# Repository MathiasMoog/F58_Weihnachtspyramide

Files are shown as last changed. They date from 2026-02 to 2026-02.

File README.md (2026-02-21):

# Antrieb und LED-Kerzen für Weihnachtspyramide

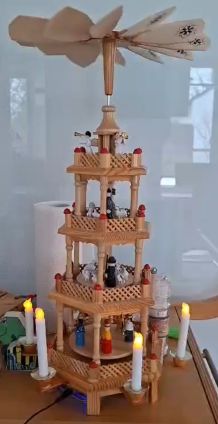
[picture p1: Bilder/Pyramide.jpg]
Weihnachtspyramide


Und als kurzes Video: [Weihnachtspyramide](Bilder/Pyramide.mp4)

## Kurzfassung

Ein Arduino Nano ESP steuert den Antrieb und die LED Kerzen einer Weihnachtspyramide.

Über den ESP wird eine MQTT Anbindung erstellt.

### Hintergrund

Unsere Weihnachtspyramide ist seit einigen Jahren nicht mehr genutzt worden, da niemand Lust hat auf die echten Kerzen aufzupassen. Außerdem läuft sie mit den Kerzen nicht so gut.

In der Bastelkiste hatte ich noch einen (uralten) [Arduino Nano ESP](https://iot.fkainka.de/board) von F. Kainka und aus dem alten Drucker den Antrieb für die Scan Einheit.

### Ordner

- Bilder - Bilder und Zeichnungen
- Druckvorlagen - OpenSCAD Zeichnungen für 3D Drucke 
- PyramidenMQTT - Der Arduino Sketch 
- PyramidenSchaltplan - KiCad Schaltplan und Platine

## Aufbau

Passt es für eure Weihnachtspyramide an, dieser Abschnitt bezieht sich auf meine Pyramide.

### Antrieb 

Mit einem Motor aus der Bastelkiste probiert. Alter Antriebsmotor aus Scanner mit Getriebe. Blech zurecht gesägt. Optische Drehzahlerfassung entfernt. Anstelle Zahnräder, einen Gummiring verwendet. Letztes Zahnrad am Motor geschliffen so dass eine Laufrille für den Gummiring entsteht.  

Adapter von Antriebsstange über Antriebsrad bis Aufnahme in Kugellager, [Antrieb](Druckvorlagen/Antrieb.scad), und eine Kugellager Halterung,[Grundplatte](Druckvorlagen/Grundplatte.scad),  in OpenScad gezeichnet. Druck in PETG. Material ist guter Kompromiss zwischen leicht auf dem alten Creatity Ender druckbar und ausreichender Festigkeit. 

Antrieb                    |  Grundplatte
:-------------------------:|:-------------------------:
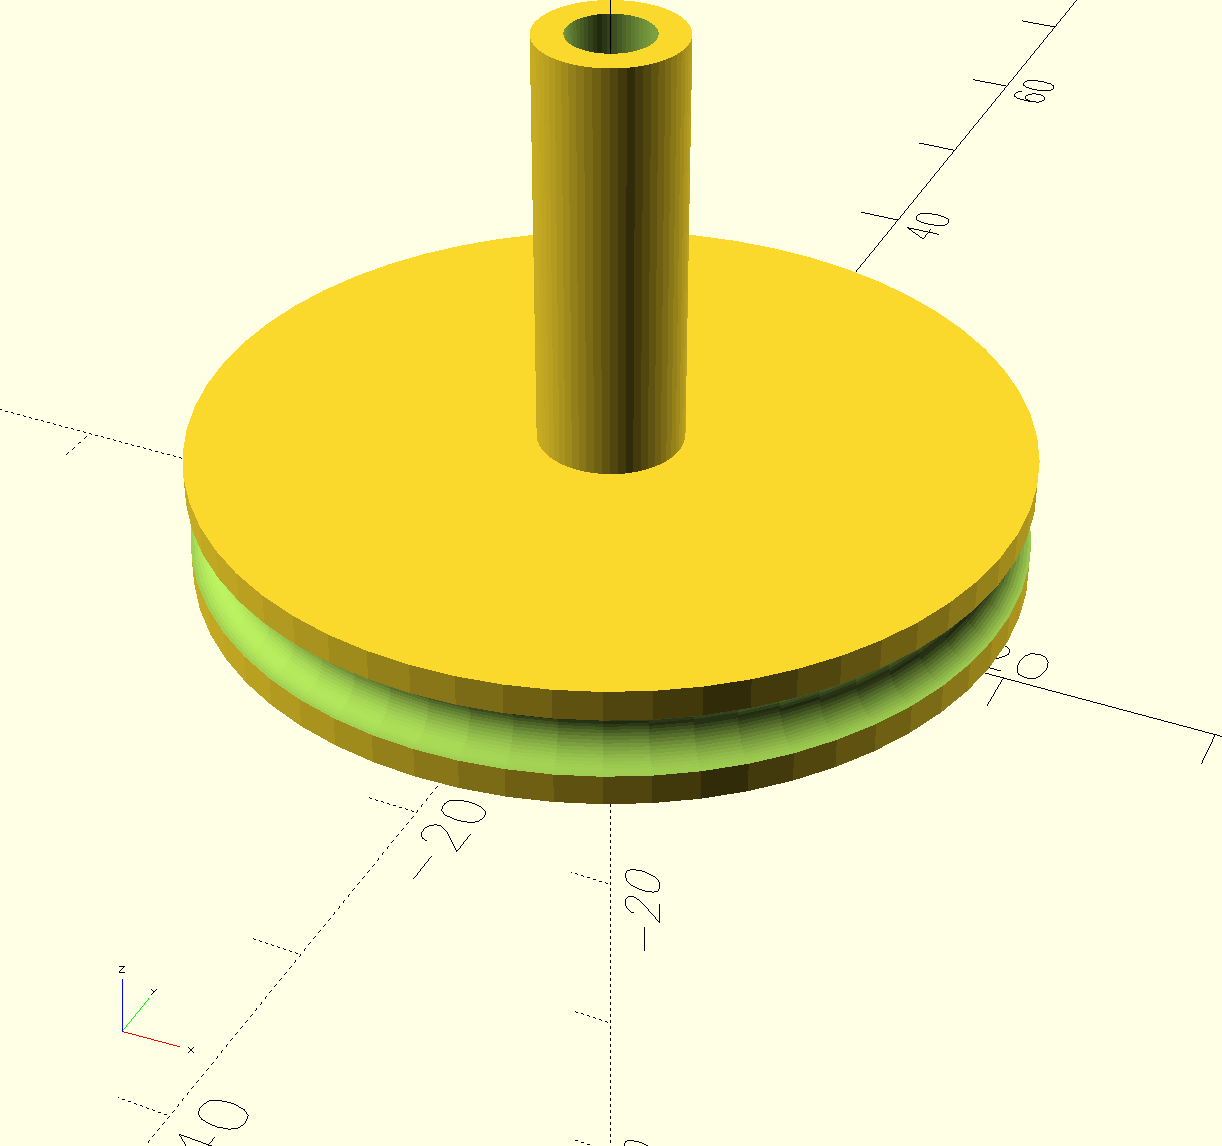
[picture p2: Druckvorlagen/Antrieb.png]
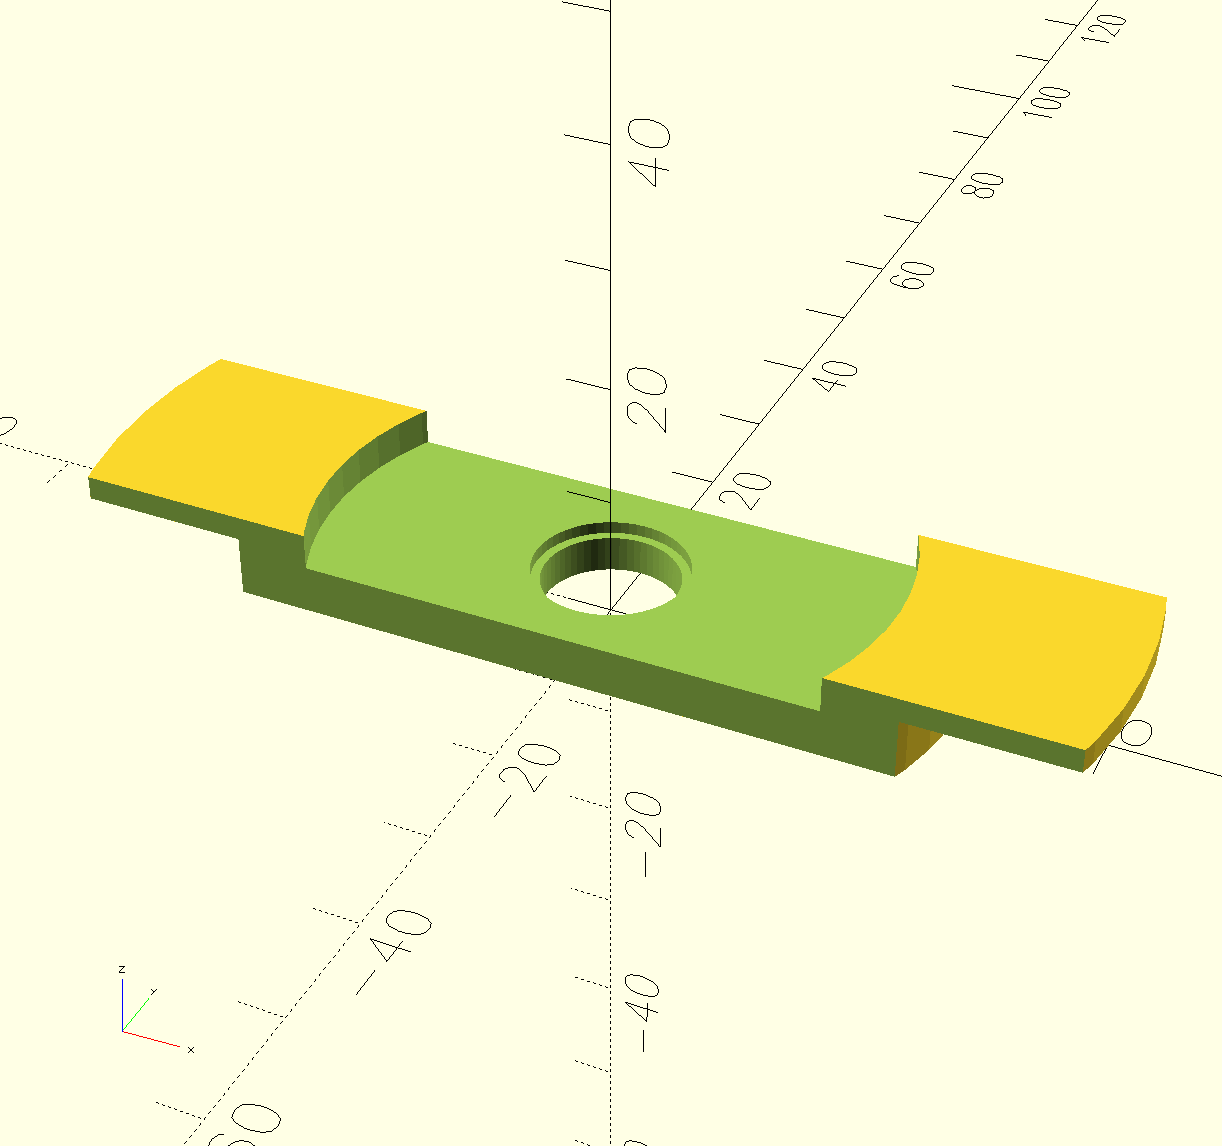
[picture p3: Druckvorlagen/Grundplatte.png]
 | 

Der neue Antrieb ersetzt die alte Lagerung in einer Keramikschale.

Vorher                    |  Nachher
:-------------------------:|:-------------------------:
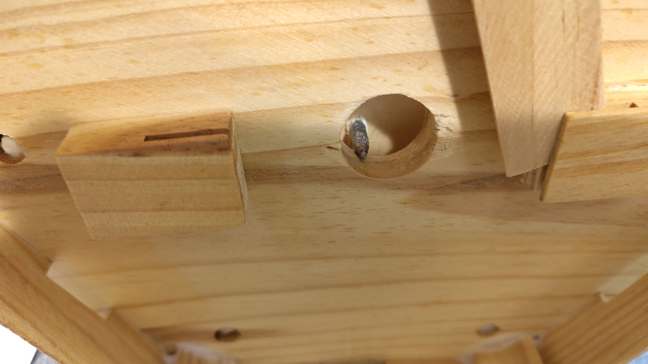
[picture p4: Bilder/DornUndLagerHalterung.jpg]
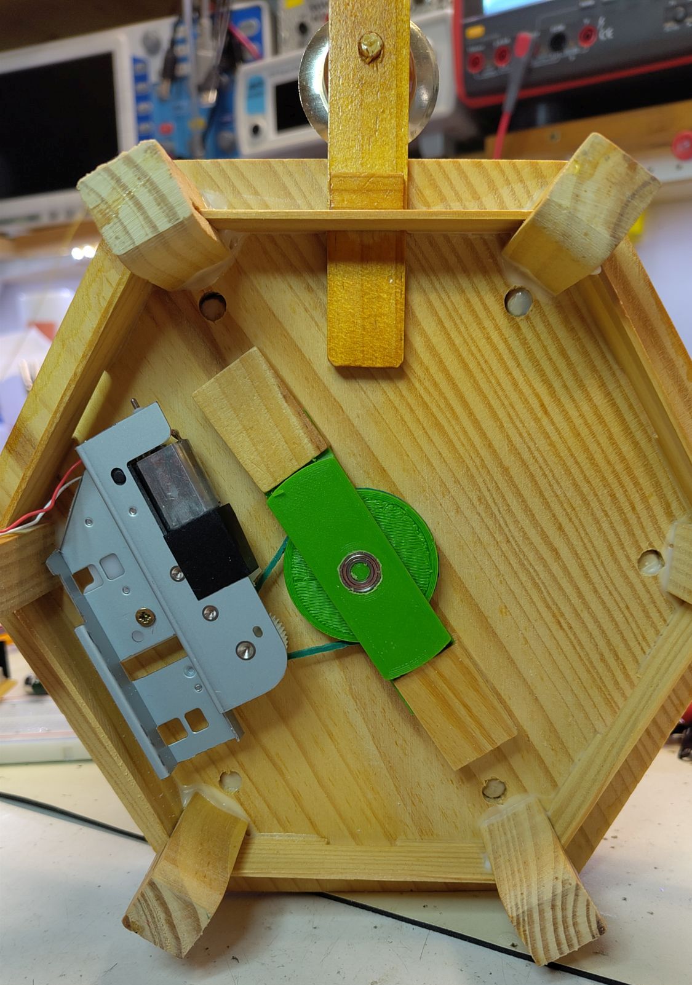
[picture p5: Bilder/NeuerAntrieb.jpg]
 | 

### Ansteuerung des Motors
  
Der Motor läuft ab 2,5 V an. Bilde 0 bis 100 auf 0 + [128, 255] ab. Er nimmt maximal 80 mA auf. Es reicht ein kleiner Transistor zum Schalten.

Aus Bastelkiste BC 639, 1 A maximal, gemessen Verstärkung hFE 100, Datenblatt mindestens 25 bei 5 mA Basisstrom. Auslegung, 560 Ohm Vorwiderstand

### Kerzen

Auf Thingiverse habe ich Kerzen mit schön gestalteten Flammen gefunden. Sie sind Teil eines Weihnachtsbogens [Christmas Light Bow](https://www.thingiverse.com/thing:4674237) von M. Lachmann. Flamme.stl mit transparentem PLA und die Kerzen in weißem PLA gedruckt. 

Kerze.stl hat Original 10 mm Durchmesser. Ich benötige 13 mm. Skaliere in x und y Richtung um 130 %. In x Richtung Skalierung 70, 80, 90, 100, 110, 120 %. Sieht nach ungleichmäßig abgebrannten Kerzen aus.

Löcher in die original Kerzenhalter gebohrt und Kabel durchgeführt:

Kabelführung                    |  Fertige Kerzen
:-------------------------:|:-------------------------:
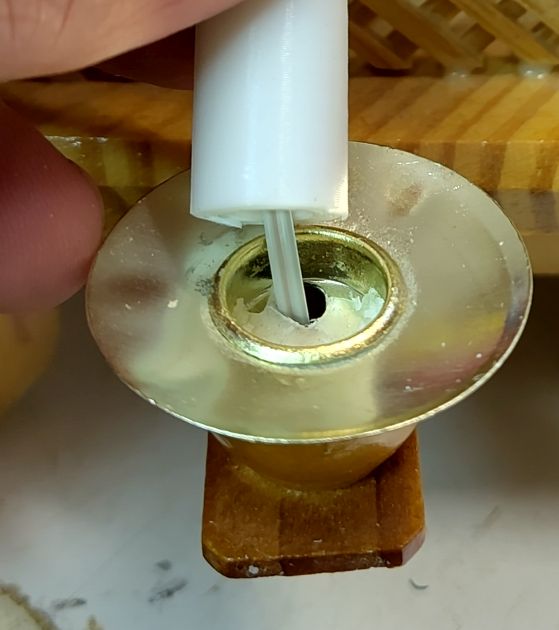
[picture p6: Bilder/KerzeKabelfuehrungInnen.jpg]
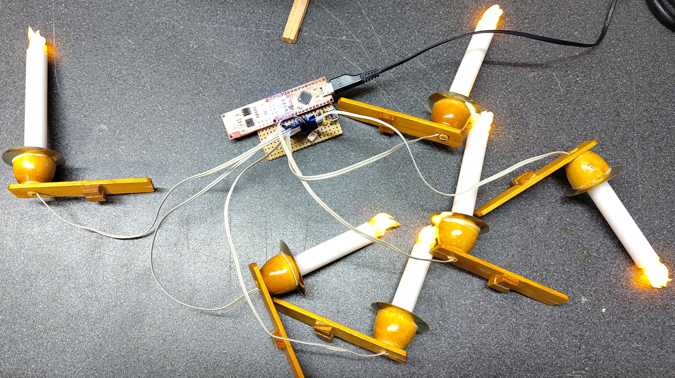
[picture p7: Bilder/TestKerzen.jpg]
 | 

An der Pyramide habe ich die Aussparungen für die Kerzenhalter mit einer Feile um deine Kabeldurchführung vergrößert.

Helle orange LEDs mit 5 mm Druchmesser im Vorrat entdeckt. Mit denen ergibt sich ein warmes Kerzenlicht. Jede LED mit zweiadrigem Kabel (Altes Flachbahn Kabel von Floppy) und 2,5 mm Stecker anbinden.

Vermessen 2,07 V bei 20 mA. Gewählt, 150 Ohm Vorwidderstand bei 5 V Versorgung und 0,5 V Spannungsabfall im ATMEGA.

## Schaltplan und Platine

Die Schaltung ist recht einfach. Motor und LEDs werden mit 5 V aus dem Arduino betrieben.

Schaltplan Weihnachtspyramide

Aufgebaut habe ich es auf einem Stück Lochraster Platine

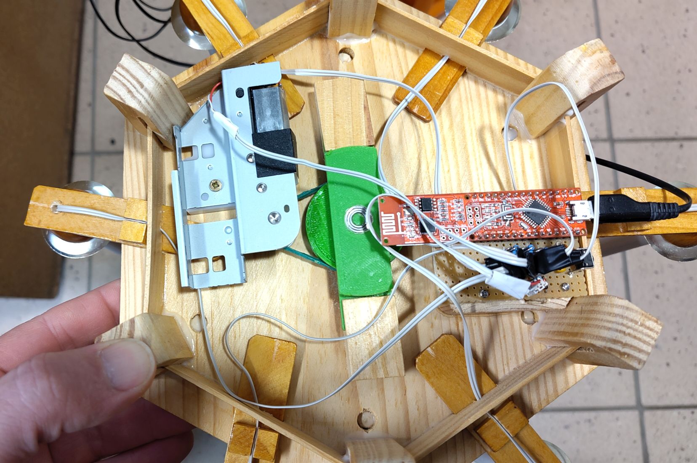
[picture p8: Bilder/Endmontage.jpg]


Der USB Anschluss und der Taster zur Bedienung ragen etwas unter dem Holzrahmen der Pyramide hervor. Mit dem Taster lassen sich die Kerzen und der Motor ein- und ausschalten.

## Arduino Sketch

Im Code erklärt: [PyramidenMqtt](PyramidenMqtt/PyramidenMqtt.ino)

Die NanoESP Boards sind schon sehr betagt, aber es funktioniert immer noch. Ich habe zwei Anpassungen an der NanoESP Bibliothek vorgenommen: Messages zuschneiden und obsolete subscribe events bei disconnect löschen. Getestet habe ich mit meinem Fork der [NanoESP Bibliothek](https://github.com/MathiasMoog/NanoESP)

Damit 6 LEDs und der Motor per PWM angesteuert werden können, nutze ich für die LEDs die [SoftPWM Bibliothek](https://github.com/bhagman/SoftPWM) von B. Hagman.

Die Konfiguration erfolgt in secrets.h. Eingecheckt ist nur die secretsVorlage.h. In secrets.h umbenennen und anpassen.

## Einbindung in die Hausautomation

Ich nutze [openHAB](https://www.openhab.org/) mit einer textuellen Konfiguration.

Hier die Thing Definition

    Thing mqtt:topic:weihnachtspyramide "Weihnachtspyramide" (mqtt:broker:myBroker) {
      Channels:
      // Motor als Dimmer, 0..100
      Type dimmer : motor "Motor" [ stateTopic="openhab/pyramide/motor/state", commandTopic="openhab/pyramide/motor/set", min=0, max=100, step=1 ]
      // Kerzen als Switch, ON / OFF
      Type switch : kerzen "Kerzen" [ stateTopic="openhab/pyramide/kerzen/state", commandTopic="openhab/pyramide/kerzen/set" ]
    } 
	
Diese gehört in eine Bridge hinein die die Verbindung zu dem MQTT broker beinhaltet.

Die Items zu den beiden channels:

    Group gMqttWeihnachtspyramide "Weihnachtspyramide" <network> (gEG_Buero)

    /* Motor der Weihnachtspyramide.
        Dimmer 0..100
        0 = Aus
        1 = Anlauf, ca. 2.5 V
        100 = Voll an
    */    
    Dimmer PyramideMotor "Motor [%d]" <network> (gMqttWeihnachtspyramide) 
      { channel="mqtt:topic:weihnachtspyramide:motor" }

    /* Kerzen der Weihnachtspyramide.
        Switch Ein/Aus, flackern sobald ein.
    */
    Switch PyramideKerzen "Kerzen" <network> (gMqttWeihnachtspyramide) 
      { channel="mqtt:topic:weihnachtspyramide:kerzen" }

So lässt sich alles vom Handy aus bedienen und die LEDs gehen mit der restlichen Weihnachtsbeleuchtung automatisch an.

## Testen

Zum Testen - und für den Betrieb - wird ein MQTT broker benötigt. Ich verwende den [Mosquitto broker](https://mosquitto.org/) von Eclipse.

Es hat etwas gedauert bis ich eine stabile Lösung mit automatischen Neu-Verbindungen zum WiFi und MQTT beisammen hatte. Ein Blick in die Mosquitto Logs hilft ...

    sudo tail -f /var/log/mosquitto/mosquitto.log

Mittlerweile gehen nur noch sehr selten (während reconnect) MQTT messages verloren, ggf. Prüfen

    mosquitto_sub -h xxx -u xxx -P xxx -t openhab/pyramide/#

## Nachbau

Den NanoESP gibt es schon länger nicht mehr. Der Arduino Nano ESP 32 ist nahezu Pin-Kompatibel. Zu beachten ist:

- Er arbeitet mit 3.3 V, ggf. die LED Vorwiderstände anpassen 
- Mein Motor benötigt 5 V, die können von USB übernommen werden
- Die SoftPWM Bibliothek ist nicht mehr notwendig
- Es wird ein anderer MQTT Client benötigt, z.B. ArduinoMqttClient

Umgesetzt habe ich es nicht, hier ein MQTT Beispiel mit dem Nano ESP 32: [MQTT LED](https://gitlab.com/MathiasMoog/L20_MqttLed)

Ansonsten irgendein günstiges ESP 32 Board ...

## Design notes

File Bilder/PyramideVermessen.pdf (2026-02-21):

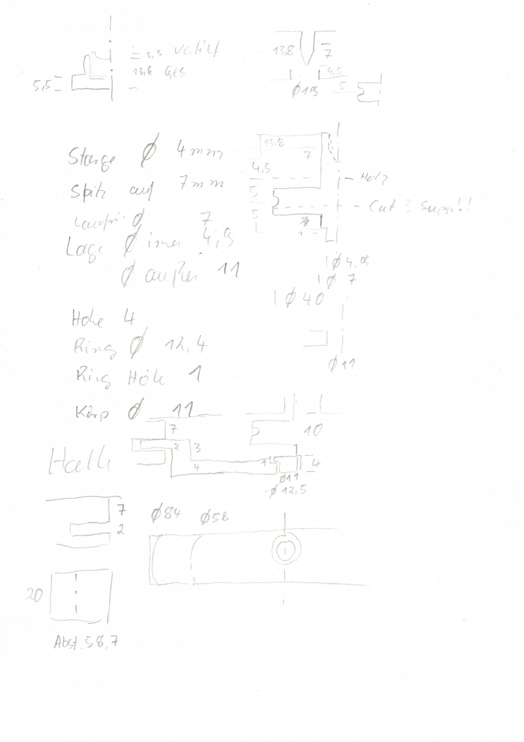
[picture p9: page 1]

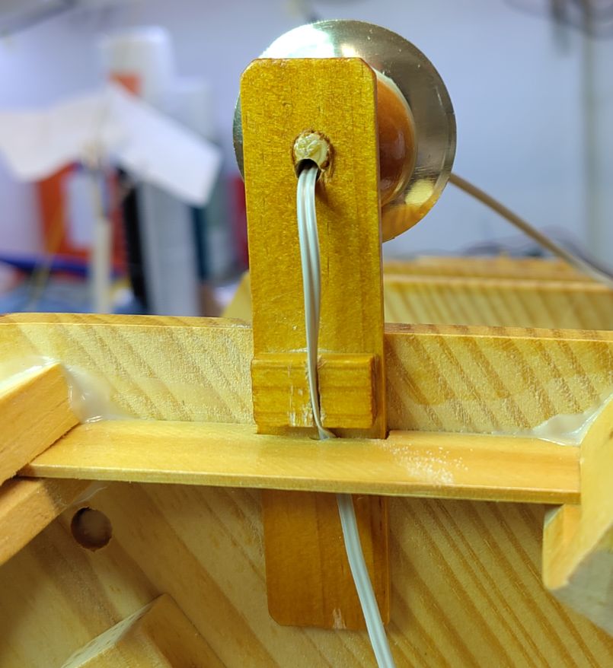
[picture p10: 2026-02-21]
Bilder/KerzeKabelfuehrungUnten.jpg

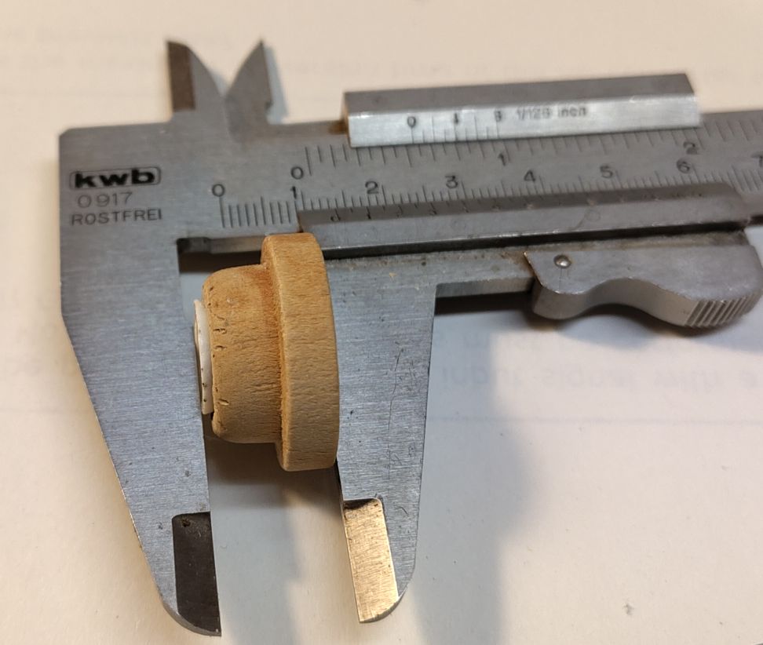
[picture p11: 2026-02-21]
Bilder/OriginalKeramikLager.jpg

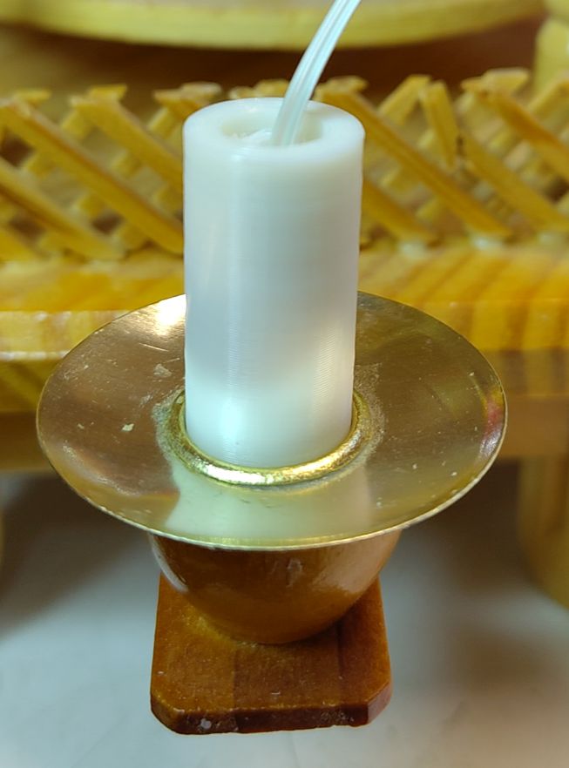
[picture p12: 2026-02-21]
Bilder/KerzeKabelfuehrungOben.jpg

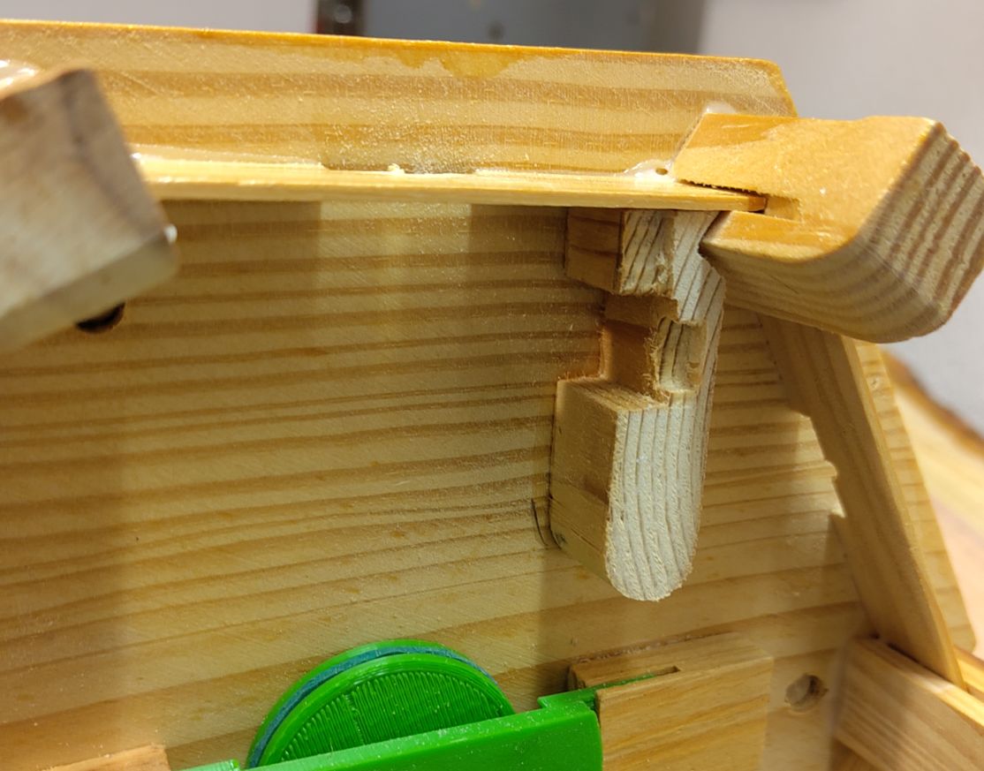
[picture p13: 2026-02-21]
Bilder/HalterungPlatine.jpg

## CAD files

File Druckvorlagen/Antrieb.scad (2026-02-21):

/* Antrieb
  Oben wird die bisherige Achse eingesetzt. 
  Unten folgt das Antriebsrad mit Vertiefung und 
  der Stift für das Lager
  
  Am besten mit Support von unten drucken.
  Lässt sich gut nacharbeiten.
  
  Druck mit ABS dmit es ordentlich hält
  
  Mathias Moog, 2026, CC BY NC SA
*/

// Schöne Rundungen
$fn=60;

/* Torus aus Anleitung
  r1 - großer Radius
  r2 - kleiner Radius
*/
module torus(r1, r2) {
  rotate_extrude(convexity = 10)
    translate([r1, 0, 0])
        circle(r = r2);
}

d_laufrad = 40;
d_gummi = 3;
d_stange = 4.1;
d_stift = 7;

difference() {
  union() {
    // Stift oben
    cylinder(h=(10+4.5+13.8), d=d_stift);
    // Stift unten für Lager
    translate([0,0,-4]) cylinder(h=4, d=4.9);
    // Laufrad
    translate([0,0,2]) cylinder(h=6, d=d_laufrad);
  }
  // Konische Aufnahme
  translate([0,0,14.5]) cylinder(h=7, d1=1, d2=d_stange);
  // Senkrechte Führung
  translate([0,0,14.5+7]) cylinder(h=10, d=d_stange);
  // Vertiefung Gummi
  translate([0,0,5]) torus(d_laufrad/2,d_gummi/2);
}  

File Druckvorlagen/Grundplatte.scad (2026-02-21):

/* Grundplatte
  Hält das Gewicht des Läufers. 
  In der Mitte ist ein Lager das das Gewicht
  aufnehmen kann.
  
  Die beiden flachen Enden halten es in der Pyramide
  
  Am besten mit Support drucken und die flachen
  Enden nachfeilen. Das ist einfacher als
  das Loch für das Lager nachzuarbeiten.
  
  Druck mit ABS dmit es ordentlich hält
  
  Mathias Moog, 2026, CC BY NC SA
*/

// Schöne Rundungen
$fn=60;

difference() {
  union() {
    // Grundplatte
    cylinder(h=7, d=58);
    // Flache Enden, angehoben
    translate([0,0,5]) cylinder(h=2, d=84);
  }
  // Auf die Breite von 20 mm zuschneiden
  translate([-50,10,-1]) cube([100,50,20]);  
  translate([-50,-60,-1]) cube([100,50,20]);
  // In der Mitte aussparen für Laufrad und Gummi
  translate([0,0,4]) cylinder(h=10, d=47);
  // Lager unten
  translate([0,0,-1]) cylinder(h=10, d=11);
  // Lager Haltering
  translate([0,0,3]) cylinder(h=10, d=12.5);
}  

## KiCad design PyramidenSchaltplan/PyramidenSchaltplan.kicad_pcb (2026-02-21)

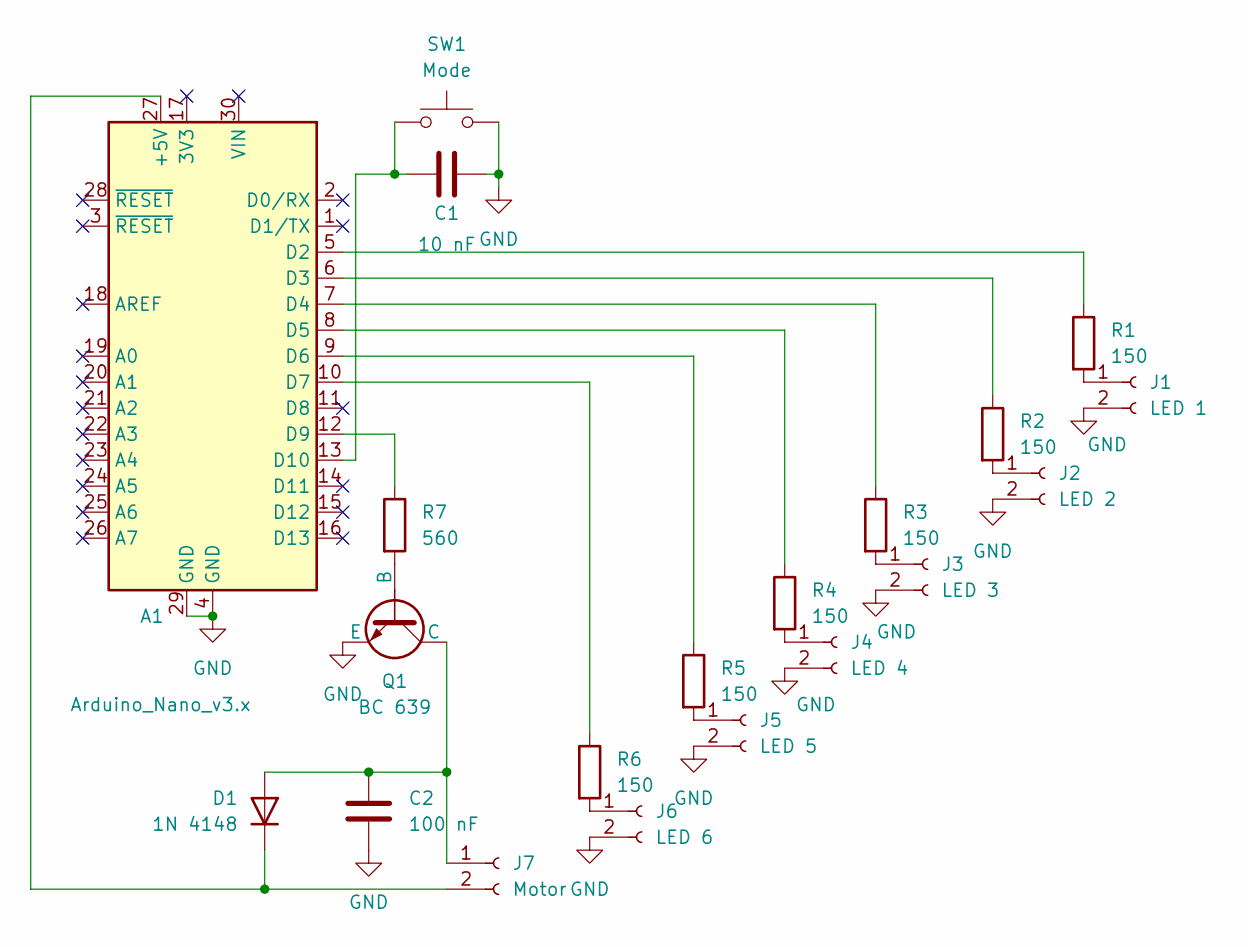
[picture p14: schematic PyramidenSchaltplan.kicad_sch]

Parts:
A1: Arduino_Nano_v3.x; Arduino_Nano
C1: 10 nF; C_Disc_D4.7mm_W2.5mm_P5.00mm
C2: 100 nF; C_Disc_D4.7mm_W2.5mm_P5.00mm
D1: 1N 4148; D_5W_P5.08mm_Vertical_AnodeUp
J1: LED 1; PinHeader_1x02_P2.54mm_Vertical
J2: LED 2; PinHeader_1x02_P2.54mm_Vertical
J3: LED 3; PinHeader_1x02_P2.54mm_Vertical
J4: LED 4; PinHeader_1x02_P2.54mm_Vertical
J5: LED 5; PinHeader_1x02_P2.54mm_Vertical
J6: LED 6; PinHeader_1x02_P2.54mm_Vertical
J7: Motor; PinHeader_1x02_P2.54mm_Vertical
Q1: BC 639; TO-92L_HandSolder
R1, R2, R3, R4, R5, R6: 150; R_Axial_DIN0207_L6.3mm_D2.5mm_P5.08mm_Vertical
R7: 560; R_Axial_DIN0207_L6.3mm_D2.5mm_P5.08mm_Vertical
SW1: Mode; SW_Tactile_SPST_Angled_PTS645Vx83-2LFS

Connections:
GND: A1.4 (GND), A1.29 (GND), C1.1, C2.2, J1.2, J2.2, J3.2, J4.2, J5.2, J6.2, Q1.1 (E), SW1.2
unnamed: A1.27 (+5V), D1.1 (K), J7.2
unnamed: A1.5 (D2), R1.1
unnamed: A1.6 (D3), R2.1
unnamed: A1.7 (D4), R3.1
unnamed: A1.8 (D5), R4.1
unnamed: A1.9 (D6), R5.1
unnamed: A1.10 (D7), R6.1
unnamed: A1.12 (D9), R7.1
unnamed: A1.13 (D10), C1.2, SW1.1
unnamed: C2.1, D1.2 (A), J7.1, Q1.2 (C)
unnamed: J1.1, R1.2
unnamed: J2.1, R2.2
unnamed: J3.1, R3.2
unnamed: J4.1, R4.2
unnamed: J5.1, R5.2
unnamed: J6.1, R6.2
unnamed: Q1.3 (B), R7.2

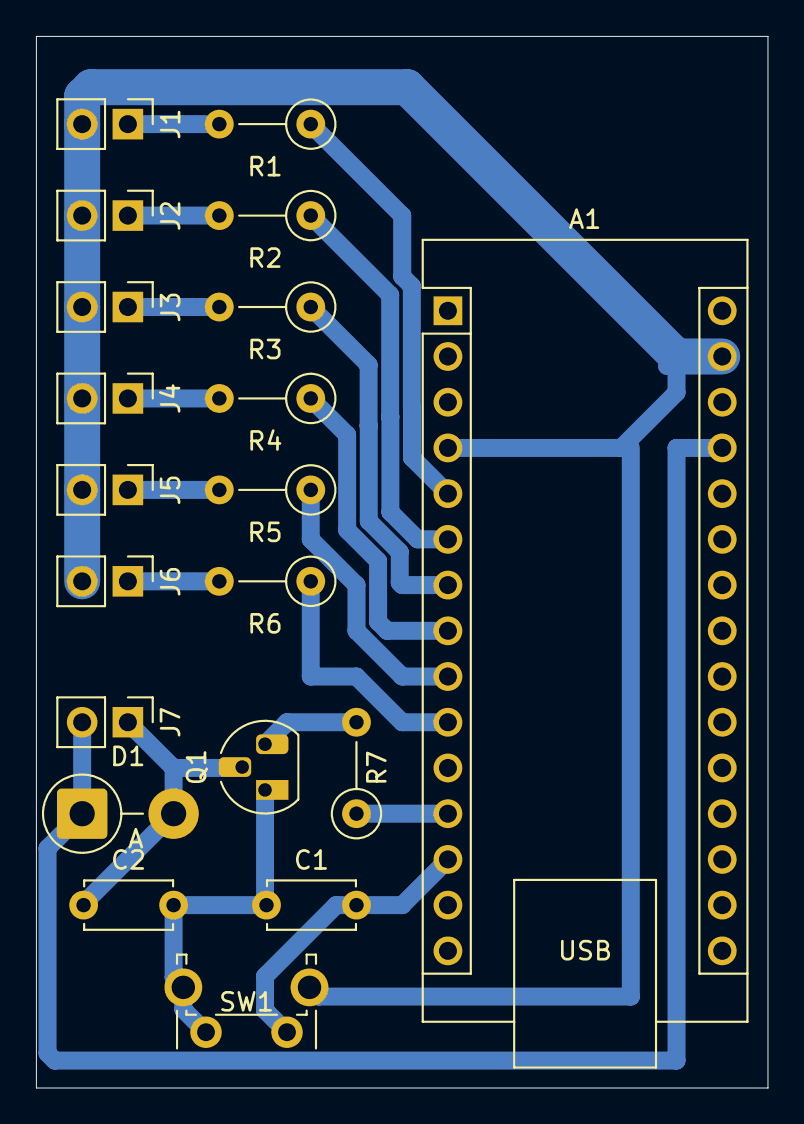
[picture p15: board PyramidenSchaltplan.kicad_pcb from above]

Board: 2 copper layers, 40.6 x 58.4 mm, 20 parts (0 on the bottom side), 18 nets.

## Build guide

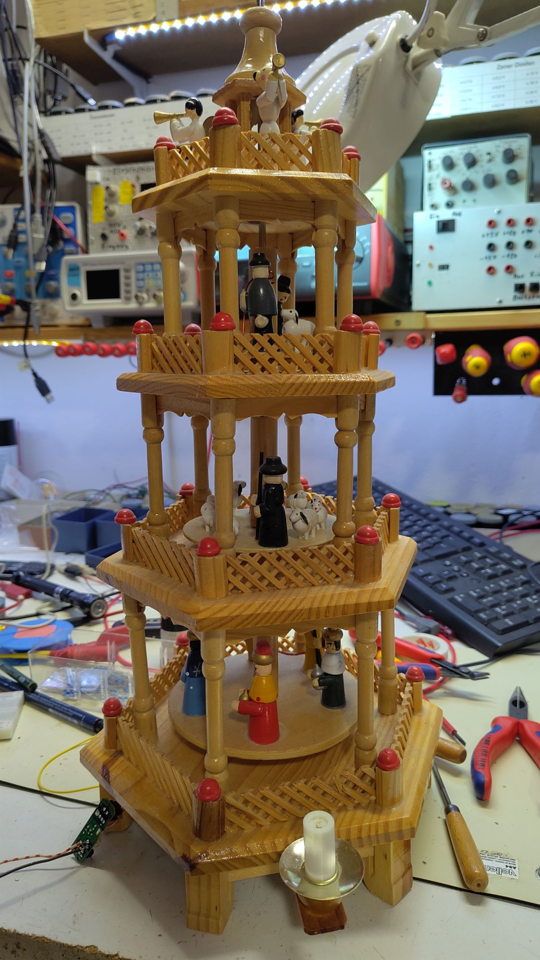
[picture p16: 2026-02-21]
Bilder/PyramideProbeinstallation.jpg

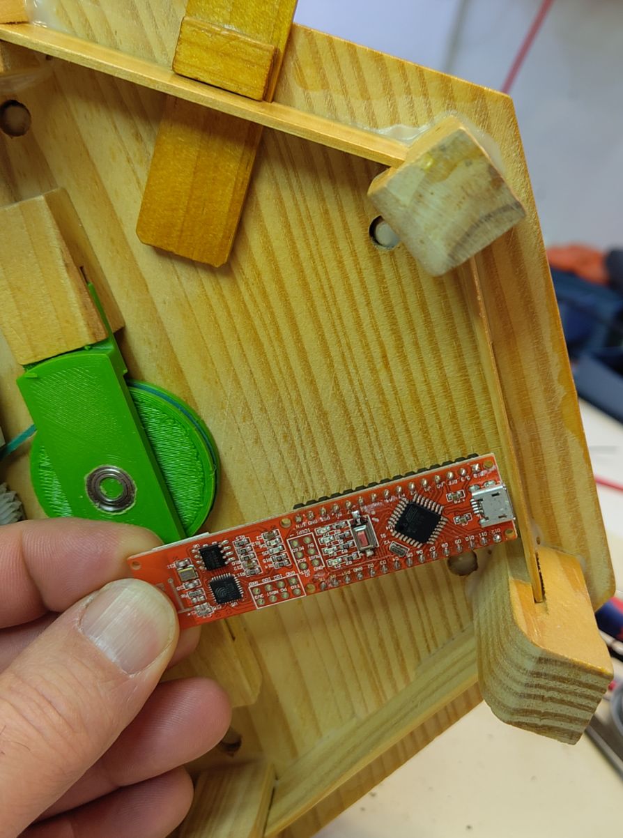
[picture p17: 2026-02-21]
Bilder/InstallationsideePrezelBoard.jpg

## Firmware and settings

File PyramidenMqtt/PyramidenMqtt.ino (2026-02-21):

/* Pyramdiden Steuerung mit MQTT

  Siehe ReadMe.md im Übergeordneten Ordner.

  Hardware:

  - Taster nach GND an PIN_TA (12)
  - Motortreiber Transistor an PIN_M (PWM, D9)
  - LEDs an den Pins D2 bis D7 im pins_led Array

  Ich habe ein altes "Prezel-Board" https://iot.fkainka.de/ von F. Kainka verwendet. 
  Zum Programmieren Nano und "Old Bootloader" anwählen.

  Software:

  Der Sketch ist in die Abschnitte
   - Kerzen
   - Motor
   - Taster 
   - MQTT 
  gegliedert.

  Die WiFi und MQTT Zugangsdaten sind in der externen secrets.h Datei.
  Eingecheckt ist nur eine leere Vorlage. Umbenennen in secrets.h und auffüllen!

  Copyright, 2026, Mathias Moog, Deutschland, CC-BY-NC-SA
*/

// -------------------------------------------------------------------------
// Genutzte Bibliotheken und lokale Header

// PWM in Software, https://github.com/bhagman/SoftPWM
#include <SoftPWM.h>
// Prezel Board Bibliothek für WLAN und MQTT, https://github.com/FKainka/NanoESP
// Nicht im Arduino Bibliotheksmanager, in das Arduino library Verzeichnis herunterladen / clonen
// Die Bibliothek ist schon betagt, es entstehen einige Warnungen beim Übersetzen
// Aktuell Bugfix in meinem Branch: https://github.com/MathiasMoog/NanoESP
#include <NanoESP.h>
#include <NanoESP_MQTT.h>
#include <SoftwareSerial.h>
// Lokale header Datei mit den Zugangsdaten und den MQTT Topics
// Eingecheckt ist nur die Vorlage secrets_vorlage.h. Umgenennen und anpassen!
#include "secrets.h"


// Loop Counter, einige aufwändige Aufgabe nur sporadisch ausführen
byte lc = 0;


/*--------------------------------------------------------------------------
  Flackernde LEDs als Kerzenersatz.

  Basierend auf der SoftPWM Bibliothek von Brett Hagman und Paul Stoffregen, Siehe https://github.com/bhagman/SoftPWM

  Es werden fortlaufende Pins, hier 2 bis 7 verwendet. Das vereinfacht den Aufbau und den Code.
*/

// LEDs von einschließlich pin_start bis einschließlich pin_end
const byte pin_start = 2;
const byte pin_end = 7;
// Anzahl der LEDs
const byte npins = pin_end - pin_start + 1;
// Loop Counter (lc) für das nächste Flackern
byte flickerLc[npins];
// Schalter zum An- und Ausschalten der Kerzen
boolean candleState = false;
// Alter Zustand des Schalters. Wird für die MQTT Status Rückmeldungen benötigt
boolean new_candleState = candleState;

// Initialisierung der Kerzen Pins und Variablen
void setupCandle() {
  for (byte i = 0; i < npins; i++) {
    SoftPWMSet(pin_start + i, 0); // Aus
    flickerLc[i] = lc + random(1, 6); // Flicker
  }
}

// Lasse die Kerzen mit flackern beginnen. Zu Beginn alle gleichzeitig mit Zufallswerten an.
void startFlicker() {
  for (byte i = 0; i < npins; i++) {
    const byte pwm = random(50, 256);
    SoftPWMSet(pin_start + i, pwm);
    flickerLc[i] = lc + random(1, 6);
  }
}

// Flackern, nur die für die flickerLc zugrifft. Prüfe candle State und schalte aus.
void flickerCandle() {
  if (candleState) {
    for (byte i = 0; i < npins; i++) {
      if (lc == flickerLc[i]) {
        const byte pwm = random(50, 256);
        SoftPWMSet(pin_start + i, pwm);
        flickerLc[i] = lc + random(1, 6);
      }
    }
  } else {
    // Switch off
    for (byte i = pin_start; i <= pin_end; i++) {
      SoftPWMSet(i, 0);
    }
  }
}

/* -----------------------------------------------------------------------------
    Antrieb der Pyramide, PWM Steuerung

    Nutzt Hardware PWM auf D9
*/

#define PIN_M 9

// Initialisierung, Motor ist aus
void setupMotor() {
  pinMode(PIN_M, OUTPUT);
  digitalWrite(PIN_M, LOW);
}

/* Ansteuerung des Motors
  Der Motor läuft erst ab ca. 2,5 V an. 

  Lösung: Über MQTT kommt von openHAB der Dimmwert als Prozent (0 bis 100)
  
  Die 0 geht auf die 0 über alle anderen Zahlen werden um 155 erhöht.
*/
void setMotor(byte percent) {
  if (percent == 0) {
    digitalWrite(PIN_M, LOW);
  } else {
    analogWrite(PIN_M, constrain(155 + percent, 0, 255));
  }
}

/* -----------------------------------------------------------------------------
    Der Taster für den manuellen Wechel der Modi

    Noch nicht fertig programmiert ...
*/
#define PIN_TA 10
// Letzter Zustand. Entprellen automatisch durch den langsamen Loop Durchlauf.
boolean ta_last_state = HIGH;

// Setup des Taster Pins
void setupTaster() {
  pinMode(PIN_TA, INPUT_PULLUP);
  ta_last_state = digitalRead(PIN_TA);
}


// Liefert true Wenn der Taster neu gedrückt wurde
boolean checkTaster() {
  const boolean s = digitalRead(PIN_TA);
  boolean ret = (s == LOW && ta_last_state == HIGH);
  ta_last_state = digitalRead(PIN_TA);
  return ret;
}


/* -----------------------------------------------------------------------------
    MQTT Anbindung

    Siehe:  https://github.com/FKainka/NanoESP/tree/master/examples/MQTT/MQTT_Basics

  Benötigt eine aktuelle Firmware. Mein altes Brezel Board hatte eine zu alte Firmware.

  Der ESP Chip ist über Software Serial an den Pins 11 und 12 angebunden.

*/

// Zugriff auf das WiFi Modul mit dem ESP
NanoESP nanoesp = NanoESP();
// MQTT für den Nano ESP
NanoESP_MQTT mqtt = NanoESP_MQTT(nanoesp);


// Eingebaute LED, signalisiert die WiFi und MQTT Verbindung. An wenn alles OK ist
const byte pin_mqtt_led = 13;
/* State: 0=b00-off (Anfangszustand), 1=b01-Nur Kerzen, 2=b10-Nur Motor, 3=b11-Kerzen und Motor
 Die Wahl ermöglich einen Abbleich mit MQTT durch bit 0 Kerzen und bit 1 Motor 
*/
byte state = 0;
// Neuer Zustand, in loop erfolgt der Zustandswechsel
byte new_state = state;
// Motor Drehzahl Einstellung mit akutellem Zustand und neuem Wert
byte motor = 100;
byte new_motor = motor;

// In den nächsten Zustand wecheln
// Wird in Verbindung mit dem Taster genutzt. Mit jedem Tastendruck der nächste Zustand
// Wenn alle durch sind beginnt es wieder von vorne.
void nextState() {
  new_state = state + 1;
  if (new_state > 3) {
    new_state = 0;
  }
}

// Motor Zustand senden, auf dem state topic
boolean publish_motor() {
  Serial.print(F("MQTT sende Motor "));
  Serial.println(motor);
  return mqtt.publish(0, TOPIC_MOTOR_STATE, String(motor));
}

// Kerzen Zustand senden, auf dem state topic
boolean publish_kerzen() {
  Serial.print(F("MQTT sende Kerzen "));
  Serial.println(candleState);
  return mqtt.publish(0, TOPIC_KERZEN_STATE, candleState ? F("ON") : F("OFF"));
}

// Callback Funktion, neue Motor Einstellungen empfangen
void callback_motor(const String& value) {
  // Wandle in zulässige Zahl um
  new_motor = constrain(value.toInt(), 0, 100);
  Serial.print(F("MQTT empfange Motor "));
  Serial.println(new_motor);
  // Die Verarbeitung erfolgt in loop, das vermeidet Hänger mit verschachtelten Funktionsaufrufen
}

// Callback Funktion, neue Kerzen Einstellungen empfangen
void callback_kerzen(const String& value) {
  // ON -> true, OFF -> false
  new_candleState = value.equals(F("ON"));  // Alles was nicht ON ist ist OFF ...
  Serial.print(F("MQTT empfange Kerzen "));
  Serial.println(new_candleState);
  // Die Verarbeitung erfolgt in loop, das vermeidet Hänger mit verschachtelten Funktionsaufrufen
}

// WIFI und MQTT Verbindung aufbauen
// Reconnect ist schwierig ...
void connect() {
  nanoesp.configWifiStation(SECRET_SSID, SECRET_PASS);
  if (nanoesp.wifiConnected()) {
    Serial.println(F("Wifi verbunden"));
    digitalWrite(pin_mqtt_led, HIGH);
    // Gib die IP Adresse aus (nur zu Debug Zwecken)
    Serial.print(F("Zugewiesene IP Adresse "));
    Serial.println(nanoesp.getIp());
  } else {
    Serial.println(F("Wifi nicht verbunden"));
    digitalWrite(pin_mqtt_led, LOW);
    return;
  }

  // MQTT Verbindung aufbauen, Startwerte in die status Felder übermitteln und die set Felder abbonieren
  // Das erste Argument ist die ID, genau wie im Beispiel zur NanoESP Bibliothek (MQTT_Basics.ino) auf 0 gesetzt.
  bool mqtt_ok = true;
  byte mqtt_trials = 0;
  do {
    mqtt_ok = true;
    if (mqtt.connect(0, MQTT_IP, MQTT_PORT, MQTT_ID, MQTT_USER, MQTT_PASS)) {
      Serial.println(F("MQTT erfolgreich verbunden"));
      mqtt_ok &= publish_motor();
      mqtt_ok &= publish_kerzen();
      delay(100);
      // Das dritte Argument ist qos ich habe es auf 2 gesetzt, a bei 0 zu viele Verluste stattfanden. 
      if (!mqtt.subscribe(0, TOPIC_MOTOR_SET, 2, callback_motor)) {
        Serial.println(F("Subscribe Fehler für Motor"));
        mqtt_ok = false;
      }
      delay(100);
      if (!mqtt.subscribe(0, TOPIC_KERZEN_SET, 2, callback_kerzen)) {
        Serial.println(F("Subscribe Fehler für Kerzen"));
        mqtt_ok = false;
      }
    } else {
      Serial.println(F("MQTT Verbindungsproblem."));
      mqtt.disconnect(0);
      delay(1000);
      mqtt_ok = false;
    }
  } while (!mqtt_ok & (mqtt_trials < 5));
  // Signalisiere den Verbindungsstatus
  digitalWrite(pin_mqtt_led, mqtt_ok);
  // Trenne die Verbindung falls es Probleme gibt
  if (!mqtt_ok) {
    mqtt.disconnect(0);
    delay(1000);
  }
}

// Initialisierung von WIFI und MQTT, nur einmal in setup
void setupMQTT() {
  // LED aktivieren
  pinMode(pin_mqtt_led, OUTPUT);
  digitalWrite(pin_mqtt_led, LOW);
  // Initialisiere den esp chip
  nanoesp.init();
  // Reduziere das Timeout der zugrundeliegenden Stream Klasse
  nanoesp.setTimeout(250);
  // Verbinde WLAN und MQTT
  connect();
}


/* -----------------------------------------------------------------------------
    Der üblich Sketch Aufbau mit setup und Loop

    Ist durch die vorangestellten Funktionen recht einfach gehalten.

*/

void setup() {
  // Serielle Debug Ausgaben
  Serial.begin(19200);
  Serial.println(F("Weihnachtspyramide mit MQTT Anbindung"));
  // Initialisiere alle Komponenten
  setupMotor();
  setupTaster();
  SoftPWMBegin();
  setupCandle();
  setupMQTT();
}


void loop() {
  // Nur in setup hatte es nicht geholfen. Setze das timeout immer wieder zurück.
  nanoesp.setTimeout(150);
  // Prüfe hin und wieder die WLAN Verbindung, die Prüfung stört den MQTT Empfang.
  if (lc == 237) {
    Serial.println(F("\nCheckWifi"));
    if (!nanoesp.wifiConnected()) {
      Serial.println(F("Reconnect WiFi"));
      connect();
    }
  }
  // Prüfe den Taster
  if (checkTaster()) {
    nextState();
  }
  // Zustandswechsel anhand es Tasters vormerken
  if (new_state != state) {
    Serial.print(F("Wechsel in Zustand "));
    Serial.println(new_state);
    switch (new_state) {
      case 0:  // Schalte alles aus
        new_candleState = false;
        new_motor = 0;
        break;
      case 1:  // Nur Kerzen
        new_candleState = true;
        new_motor = 0;
        break;
      case 2:  // Nur Motor
        new_candleState = false;
        if (motor == 0) {
          new_motor = 100;  // Default ...
        }
        break;
      case 3:  // Kerzen und Motor
        new_candleState = true;
        if (motor == 0) {
          new_motor = 100;  // Default ...
        }
        break;
    }
    state = new_state;
  }

  // Zustandswechsel der Kerzen abarbeiten
  if (candleState != new_candleState) {
    Serial.print(F("Neuer Zustand Kerzen "));
    Serial.println(new_candleState);
    // Akzeptiere den Wechsel, Flackern erfolgt automatisch
    candleState = new_candleState;
    // Kerzen starten
    if (candleState) {
      startFlicker();
    }
    // Aktualisiere MQTT
    publish_kerzen();
    // Aktualisiere den Taster Zustand, vermeide unnötiges doppeltes Update
    bitWrite(state, 0, candleState);
    new_state = state;
  }

  // Zustandswechsel des Motors abarbeiten
  if (motor != new_motor) {
    Serial.print(F("Neuer Zustand Motor "));
    Serial.println(new_motor);
    // Akzeptiere den Wechsel
    motor = new_motor;
    // Setze den Zustand
    setMotor(motor);
    // Aktualisiere MQTT
    publish_motor();
    // Aktualisiere den Taster Zustand, vermeide unnötiges doppeltes Update
    bitWrite(state, 1, motor > 0);
    new_state = state;
  }

  // regelmäßige Aufgaben abarbeiten
  flickerCandle();  // Lass die Kerzen flackern falls gewünscht
  // Nachrichten Empfangen und die passendne Funktionen aufrufen
  // Sehr knauserig mit dem buffer sein. Die Implementierung in NanoESP_MQTT.cpp ist speicher intensiv mit mehreren Strings.
  // Der recv Aufruf benötigt etwa eine Sekunde
  // Ein if (nanoesp.available()) ist nicht zielführend, es arbeitet nicht zuverlässig.
  mqtt.recvMQTT(0, 40);

  // Sende hin und wieder in Ping, das Ping dauert und stört den MQTT Empfang, daher nicht zu oft.
  if (lc % 64 == 0) {
    Serial.println(F(""));// Zeilenumbruch, dann ist es gut erkennbar.
    if (!mqtt.ping(0)) {
      // Irgendwas ist falsch. Besser mal neu verbinden.
      Serial.println("MQTT Verbindung verloren. Erneuere!");
      mqtt.disconnect(0);
      connect();
    }
  }
  lc++;
  Serial.print(F("."));
}

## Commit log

2026-02-21 Pyramide einsatzbereit
    [Antrieb.scad, Grundplatte.scad, PyramidenSchaltplan.kicad_pcb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]
2026-02-21 Update title to include LED in README
